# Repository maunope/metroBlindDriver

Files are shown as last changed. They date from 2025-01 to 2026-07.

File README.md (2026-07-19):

# Disclaimer
This is still a prototype; the circuit design was built and tested on a perfboard, the KiCad board design was never tested. Use at your own risk and plz **don't come whining if you damage stuff or set your house on fire.**

# WARNING
This project entails working with a 220V powered device with a metal chassis and **no grounding**. These devices are 40+ years old and saw lots of abuse; wire insulation may fail, and motor windings may short circuit. Before wiring anything up, check impedance between the chassis, the engine hull, and all contacts carrying 220V power; anything below 2 megaohms means insulation needs to be re-checked. 
Consider wiring the blind chassis to the ground line for additional safety.

# Metro Blinds Driver

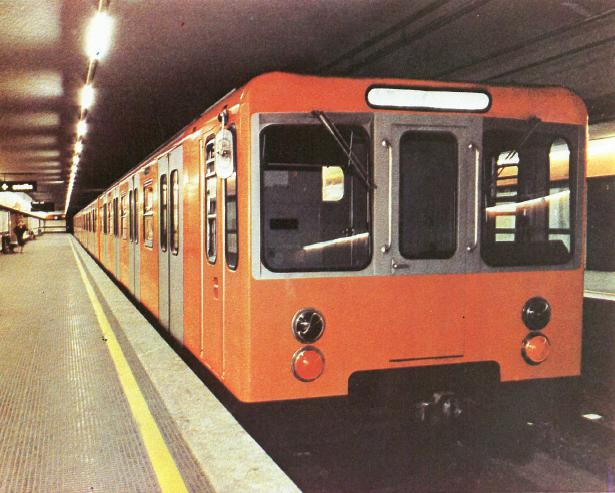
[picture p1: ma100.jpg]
Actotral MA100 vintage photo


Arduino-based driver board to control Acotral MA100 electric locomotives' front and side stops blinds.

Acotral MA100s were first issued to Rome's **"A"** metro line where they were in service between 1980 and 2005, before being overhauled/modified and reassigned to the Roma Lido line until their decommissioning in 2018. 

[Trasporti di Roma](https://romaatac.altervista.org/mezzi-di-roma/ma-100/)
[Wikipedia](https://it.wikipedia.org/wiki/Elettromotrici_ACOTRAL_MA_100)

Stops signaling blinds coming from wagon dismantling started circulating among flip clock collectors and have become a somewhat common find on online marketplaces.

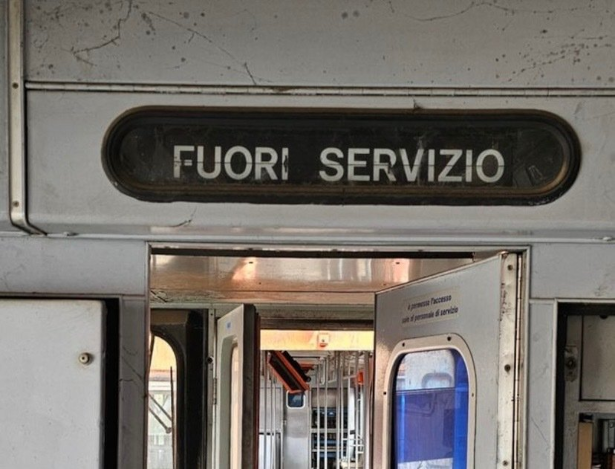
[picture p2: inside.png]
Actotral MA100 inside


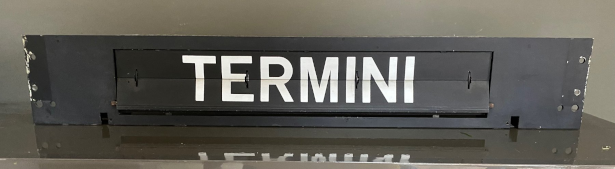
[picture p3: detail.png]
Actotral blind detail


Blinds are controlled through a 7-bit string identifying stops and are powered at 110V AC (motor) / 48V DC (control). This project emulates original locomotive control signals to drive them and display stops.

The board design in this project runs 5V DC control signals and 220V power; it requires minimal modifications to the original blinds' wiring. It is fairly easy, however, to adapt it to run 48V/110V to 100% preserve the integrity of the original wiring.

## Main features   
- Runs through stops using the blind's internal motor
- Allows manual stop selection or programmed stops sequence mode
- Allows saving configurations to the Arduino EEPROM
- Implements several controls to prevent damage/overheating in case of malfunctions

## Lateral blind design
The `LATERAL_BLIND` compile flag enables a command table built for smaller punched rollers found on side-mounted train blinds. This mode is intended to address blinds with smaller punched rollers, those mounted on the side of trains rather than the larger frontal rollers.

On the specimen I tested, the pinout was different compared to the larger frontal roller, but this may not always be true. If your roller is different, you may need to recreate the command array for your exact roller.

## Manual vs. Program mode

In **manual mode** (default), stops are selected through serial port commands or single button presses. The board LED is lit during Manual mode. 

**Program mode** automatically loops a sequence of stops, one step every hour by default. The program will be resumed from the last reached stop in case of power OFF/ON; the hourly step timer will be reset. The board LED is off during Program mode.

To switch between modes, either use serial commands or press the board button for **3 seconds**. 

## Dependencies

- EEPROM (comes with Arduino IDE)
- [Rocket Scream Low Power](https://github.com/rocketscream/Low-Power)

## Arduino circuit board

Check the schematic in this repo; I've built and tested it on perfboard. The board design might not be 100% correct, and the layout could definitely use some improvement.

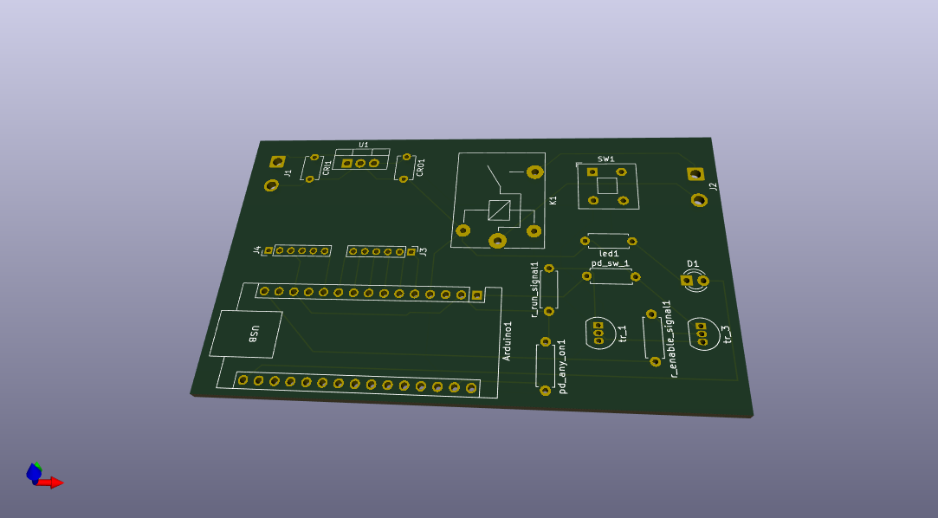
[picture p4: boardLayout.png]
Arduino Board layout


**How to read LED signals**

Either for good or bad news, the Arduino board LED will flash. 

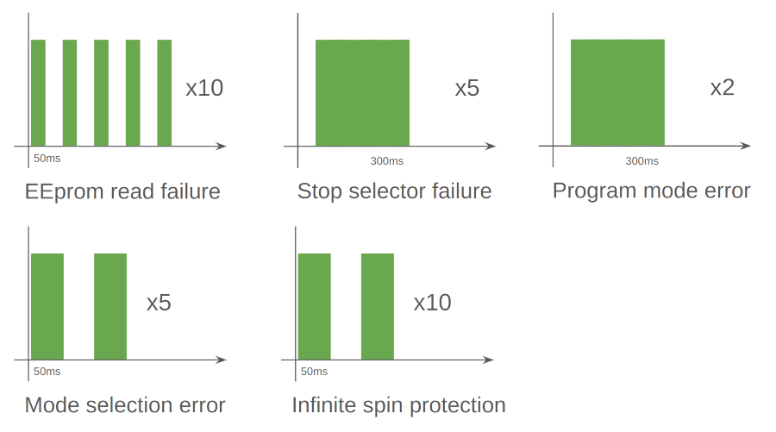
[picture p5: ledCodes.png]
Led error codes


## Original electromechanical control logic 

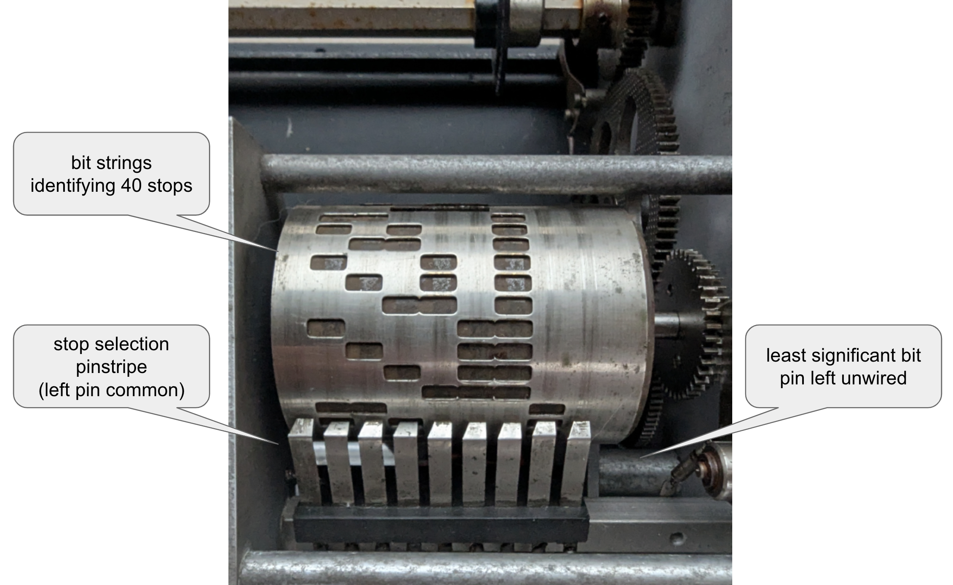
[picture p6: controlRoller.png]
Control roller detail


A punched roller is used to encode 40 unique blind positions. When a string of bits is applied to the pinstripe, the motor spins until the holes combination under the pinstripe matches powered pins, i.e.:

- **0b00111000** bit string corresponding to Termini station is applied to the pinstripe, powering pins 4, 5, 6 from the left (1st left pin is common)
- **0b0011110** bit string on the control roller is under the pinstripe; current flows through pins 4, 5, 6, and the motor spins
- Next roller bit string is **0b0100110** on the control roller; current flows through pin 6, and the motor keeps spinning
- The roller bit string is now **0b11000111**; all 1s on the pinstripe match a 0 on the roller, no current flows, the motor **stops** and will remain still until a different bit string is selected.

The original control board has 7 control pins, 2 relay coil pins, and 2 motor power pins, exposed through a DIN 41622 male connector on the side or back panel.

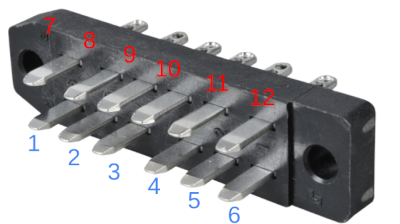
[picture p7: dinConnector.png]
Din connector detail


The original wiring:
- Pin 1-6 and 12: stop selection bit string
- Pin 11: unwired
- Pin 10: 110V AC to relay interrupted line
- Pin 9: Relay coil (+48V signal from selection roller return line)
- Pin 8: Relay coil N
- Pin 7: 110V returning from motor

## Blind Board schematic and modifications

The blind board schematic is available in "metroBlindDriver blind board" KiCad design:

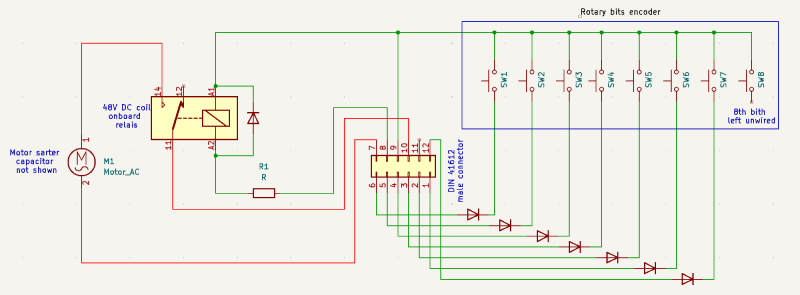
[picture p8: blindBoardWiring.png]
Original blind schematic


In the original blind design, 48V DC bits would be fed into pins 1-6 and 12; they would reach the control roller through diodes and would power the 48V relay coil through the roller common pin until the desired stop was reached. 

The original blind wiring can be easily modified to accept standard household 220V AC power and 5V DC signals.

**IMPORTANT**: Don't use this board design with 48V signals to avoid damage and fire hazard!

**IMPORTANT**: Don't run 220V AC through the motor before its coils are wired in series to avoid damage and fire hazard!

**220V AC motor wiring** Wire the motor as shown in the picture below to drive it with 220V AC power. Plastic motor caps on most (all?) blinds have diagrams explaining how to wire coils in series/parallel.
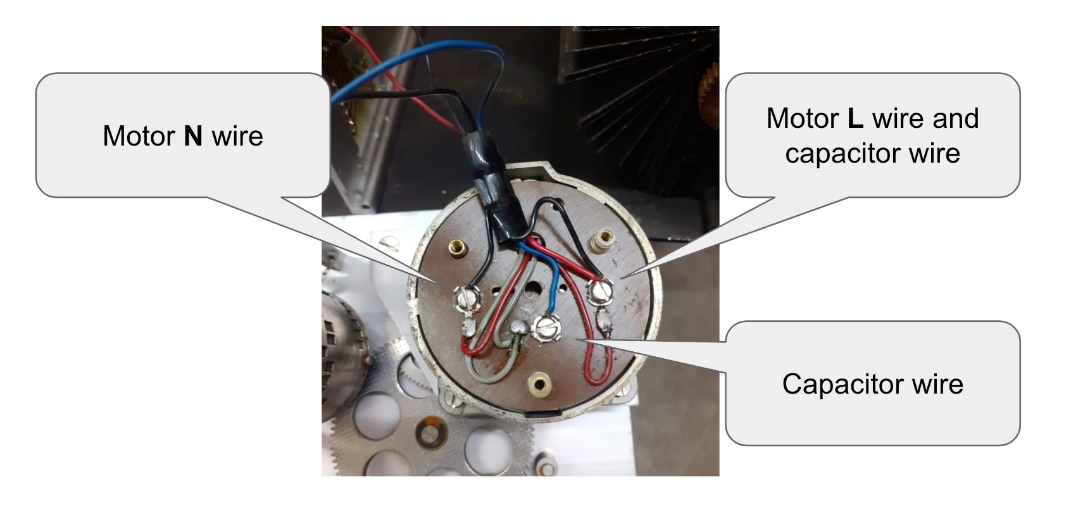
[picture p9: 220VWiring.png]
220V motor wiring detail


**5V DC external relay wiring**

To bypass the 48V coil and use an external relay, clip the motor **N** wire from the connector board trace (board end, not motor end!) and solder it to the top left pin on the DIN connector. If in doubt, use the only pin trace with no wires attached. 

Replacing the original 48V relay with a 5V or 12V one isn't sufficient, as the coil has a 4kohm resistor wired in series; plus, compatible relays are out of production, hard to source, and quite expensive. 

I wanted to preserve the original circuitry as much as possible, but definitely didn't want to faff with 48V signals.
I figured since I had already wired the motor for 220V AC, another small modification wouldn't matter much, and moving a wire to a different pin seemed way less invasive than replacing a relay and a big *ss resistor.
You might want to do things differently here; the circuit is easy enough to work with, these are just my 2c :-) 

Rewired schematic below:

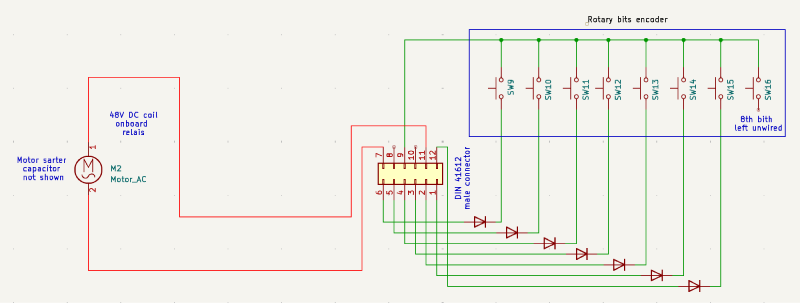
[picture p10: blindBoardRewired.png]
Original blind schematic


The new wiring:
- Pin 1-6 and 12: 5V bit string
- Pin 11: to motor relay NO contact on Arduino board
- Pin 10: unwired, can be used to ground the blind chassis
- Pin 9: to Arduino "Any Running" pin
- Pin 8: unwired
- Pin 7: to motor relay NO contact on Arduino board

## How to install and adjust

**First things first, let's not fry stuff**

- Check wirings and voltages
- **Mandatory**: rewire the blind board to use an external 5V relay; **don't use 48V signals with this Arduino board design!**
- **Optional**: rewire the motor to run on 220V AC; if you happen to have a 110V AC power source, that will work fine
- Wire the DIN connector pins; be sure not to short circuit anything
- Power the board and the motor **L** wire
 **No smoke? Good.**

By default, the controller will wait for commands in manual mode with the board LED **ON**.

- Press the board button briefly; the blind should roll one stop forward
- (Optional) press the board button for 3 seconds to switch to Program mode

## Push buttons commands

- **Brief press:** move one stop forward
- **3 seconds press:** switch between Manual and Program mode

## Serial port commands

Commands format: **(<<|>>)[A-Z,0-9]+**

- **<<** to read info, **>>** to set
- Command name, in caps
- (Where applicable) parameters

One command per line; the parser is pretty crude, please stick to tested commands ;-) 

**Available commands**:

- **>>GO[0-9][0-9]** select stop by zero-padded two-digit number, 01-40 (only works in manual mode)
- **>>(stop name)** (i.e., >>ANAGNINA, >>CINECITTA) select stop by name (only works in manual mode)
- **>>STOP** halt the motor
- **>>RUN** continuously run the motor 
- **>>PROGRAMSTEPSSECONDS[0-9]{4}** write steps duration for program mode, zero-padded four digits
- **<<PROGRAMSTEPSSECONDS** read steps duration for program mode
- **>>DEFAULTPROGRAM** load the default stops program to memory
- **>>PROGRAMSTOPS[0-9][0-9](?:[0-9][0-9]){0,39}** write program mode stops sequence, zero terminated, up to 40 zero-padded two-digit positive integers. The sequence is required to be ascending (i.e., 1-2-3 valid, 1-3-2 not valid)
- **<<PROGRAMSTOPS** print the program stops sequence currently in memory
- **>>PROGRAMMODE** switch to Program mode
- **>>MANUALMODE** switch to Manual mode (default)
- **>>RESETDEFAULTS** reset default configuration 
- **<<EEPROMDATA** print current eeprom conf
- **>>EEPROMDATA** write current conf from ram to eeprom
- **<<POSITION** print the current blind roller position
- **<<COMPILEDATETIME** print the sketch build timestamp

## Build flags

-DEBUG_MODE enable serial port debug messages, disable sleep mode

## Unreachable stops

The control roller pinstripe 8 signals encode 40 unique bit strings, each with three raised bits (i.e., 0b11001000, 0b00110010). This allows moving from any stop to any other by applying the destination code bit string to stop selection pins. 

At least, this is how the control roller would work hadn't its original designers decided to leave the rightmost pin unwired.

As a result, 5 out of 40 stops are encoded by only 2 wired pins and only work when selected starting from the 13 stops right behind them. 
The matrix below highlights misencoded stops and the stops that would be wrongly displayed when their code is used, i.e.:

- The blind displays stop **2** (code **0b1000110**)
- Stop **21** (code **0b1100000**) is selected
- The blind spins until stop **6**, (code **0b1100001**)
- The bitwise "(input bit string) **AND NOT** (roller bit string)" of stops **21** and **6** codes is 0 -> the relay coil is not powered
- The blind stopped on stop **6** before reaching **21** and would halt on 26, 27, 30 and 37 due to the same reason
- (**Note:** code **0b1100000** correctly drives the blind to stop **21** starting from stops 7-20)

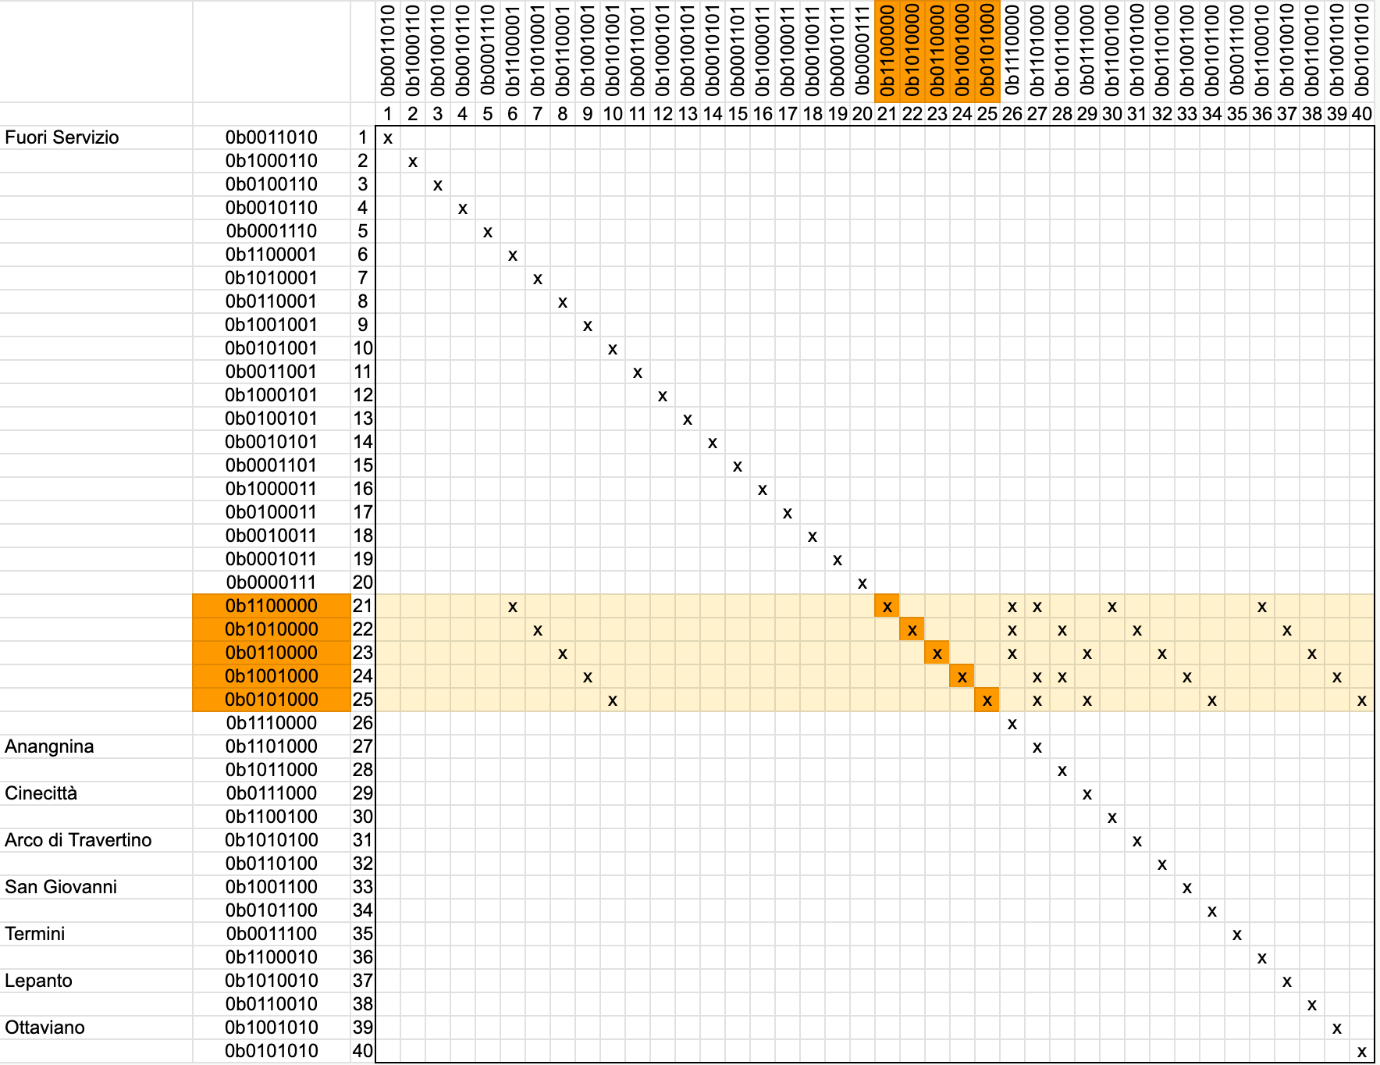
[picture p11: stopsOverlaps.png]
Overlapping stop codes table


This behavior **did not** affect actual service on Roma Metro **A** as the 5 impacted stops were blank. I decided to leave it unchanged as an interesting quirk of the original design; you might want to fix it if you plan to display anything on stops 21-25 :-D 

## Troubleshooting

**Q:** I can't tell what's going on with EEPROM data.

**A:** The <<EEPROMDATA command can extract all the info saved on the EEPROM.

**Q:** I keep getting "nonexistent stop" error.

**A:** Check wiring; any short circuit? Any missing wire? 

**Q:** Motor buzzes and doesn't spin! What's wrong?

**A:** Have you rewired the motor correctly? 

**Q:** I rebooted the board, and all my configurations are lost.

**A:** Run >>EEPROMDATA to persist configuration on EEPROM.

**Q:** I have disassembled the punched roller and now it doesn't stop on the right positions.

**A:** If the roller is misaligned, it will not work correctly. The solution is to disassemble it again, align it to the right stop, and reassemble it. It is possible to fine tune it by undoing the screw on the roller side and moving the outer plate slightly.

**Q:** That PCB design is **lame**!

**A:** It is. Any help much appreciated! ;-)

## Todo
- Readme completion
- Circuit board layout improvement

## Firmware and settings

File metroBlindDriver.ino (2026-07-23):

#include <LowPower.h>                //https://github.com/rocketscream/Low-Power
#include <EEPROM.h>

// Uncomment the next line to switch to the lateral-blind command table.
#define LATERAL_BLIND
//#define DEBUG_MODE



#ifdef LATERAL_BLIND
const int MAX_STOPS = 30;
#else
const int MAX_STOPS = 40;
#endif



struct ProgramModeStatus
{
  //current program mode position index to be displayed
  int programPos = -1;
  //last succesfully displayed destination
  int lastReachedProgramPos = -1;
  //last recorded movement millis
  unsigned long lastMovementMillis = 0;
  byte stops[MAX_STOPS] = {};
  byte stopsLength = 0;
  int stepsSeconds = -1;
};


struct ManualModeStatus
{
  //manual mode status variables
  int lastReachedManualStop = -1;
};

struct Signals
{
  //bit string currently set on output pins
  byte bitString = 0b00000000;
  //manual/program mode
  int mode = -1;
  //motion enabled status,
  bool motionEnabled = false;
};

struct EEpromData
{
  int mode = -1;
  byte programStops[MAX_STOPS];
  byte programLength = 0;
  int programStepsSeconds = -1;
};



//debug mode redirects stdout to the serial port, this avoids the need for strings buffering
#ifdef DEBUG_MODE
// Define a custom putchar function to redirect output to Serial
int putCharToSerial(char c, FILE *stream) {
  if (stream == stdout) { // Check if it's standard output
    Serial.write(c);
  }
  return 0;
}

// Declare a FILE stream for stdout (no initializer here!)
FILE customStdOut;
//printf macro, together with putCharToSerial driver debug messages straight to the Serial port,
//stores string in Program Memory and appends a new line to each log line automatically
#define DEBUG_PRINTF(format, ...) printf_P(PSTR(format "\n"),##__VA_ARGS__);
#endif

#ifndef DEBUG_MODE
#define DEBUG_PRINTF(format, ...) // Nothing 
#endif

//automatic program based movement or manual stop selection
const int MANUAL_MODE = 0;
const int PROGRAM_MODE = 1;



//8 bits strings corresponding to each Roma Metropolitana A blind position
//rightmost bit is not relevant as the corresponding pin on the blind bit strings roller is not connected
//sorting mirrors the punch hole roller's, first element selection ("Fuori Servizio") is arbitrary
//first (0000000) and last (1111111) strings are "set all pins LOW/HIGH" commands, which have no correspondance on the roller
//NOTE: the two COMMANDS[] tables below  use different byte values for the same stop names.
//We double-checked the stop codes and they are not just reversed or simple bit-shifted variants of each other;
//they are different encodings between the two branches, so the code must keep both tables separate.

#ifdef LATERAL_BLIND
const byte COMMANDS[] = {
  0b00000000,  // 00 (Stop the blind, wherever it is)
  0b01001010, //1 ANAGNINA
  0b00101010, //2
  0b00011010, //3 CINECITTA
  0b11100000, //4
  0b11010000, //5 ARCODEITRAVERTINO
  0b10110000, //6 
  0b01110000, //7 SANGIOVANNI 
  0b11001000, //8
  0b10101000, //9 TERMINI
  0b01101000, //10
  0b10011000, //11 LEPANTO
  0b01011000, //12
  0b00111000, //13 OTTAVIANO
  0b11000100, //14 
  0b10100100, //15 FUORI SERVIZIO
  0b01100100, //16 BUONE
  0b10010100, //17 
  0b01010100, //18 BUONE
  0b00110100, //19 VACANZE
  0b10001100, //20 
  0b01001100, //21 ANCHE A TE
  0b00101100, //22 E FAMIGLIA
  0b00011100, //23 
  0b11000010, //24 
  0b10100010, //25
  0b01100010, //26
  0b10010010, //27
  0b01010010, //28
  0b00110010, //29
  0b10001010, //30
  0b11111111   // 31 (Run the blind, wherever it is)
};
const int COMMANDSLEN = 32;
const int STOP = 0;
const int ANAGNINA = 1;
const int CINECITTA = 3;
const int ARCODITRAVERTINO = 5;
const int SANGIOVANNI = 7;
const int TERMINI = 9;
const int LEPANTO = 11;
const int OTTAVIANO = 13;
const int FUORISERVIZIO = 15;
const int RUN = 31;

//19 BUONE
//20 VACANZE
//22 ANCHE A TE
//23 E FAMIGLIA

#else
const byte COMMANDS[]  = {
  0b00000000,  // 00 (Stop the blind, wherever it is)
  0b00110100,  // 01 Fuori servizio 
  0b10001100, 0b01001100, 0b00101100, 0b00011100, 0b11000010, 0b10100010, 0b01100010, 0b10010010, //02-26 blank  space
  0b01010010, 0b00110010, 0b10001010, 0b01001010, 0b00101010, 0b00011010, 0b10000110, 0b01000110,
  0b00100110, 0b00010110, 0b00001110, 0b11000000, 0b10100000, 0b01100000, 0b10010000, 0b01010000,
  0b11100000,
  0b11010000,  // 27 Anagnina
  0b10110000,
  0b01110000,  // 29 Cinecittà
  0b11001000,
  0b10101000,  // 31 Arco di Travertino 
  0b01101000,
  0b10011000,  // 33 San giovanni 
  0b01011000,
  0b00111000,  // 35 Termini 
  0b11000100,
  0b10100100,  // 37 Lepanto 
  0b01100100,
  0b10010100,  // 39 Ottaviano 
  0b01010100,
  0b11111111   // 41 (Run the blind, wherever it is)
};
//the blind has 40 stops, and this is going to change :-)
const int COMMANDSLEN = 41;

//indexes of Roma Metropolitana A stops
const int STOP = 0;
const int FUORISERVIZIO = 1;
const int ANAGNINA = 27;
const int CINECITTA = 29;
const int ARCODITRAVERTINO = 31;
const int SANGIOVANNI = 33;
const int TERMINI = 35;
const int LEPANTO = 37;
const int OTTAVIANO = 39;
const int RUN = 41;
#endif

//map pins to bit string positions, 0 ot 6
//const int PIN_MAP[] = { 3, 4, 5, 6, 7, 8, 9 };
const int PIN_MAP[] = { 9, 8, 7, 6, 5, 4, 3 };

//10 seconds are approx. 2.5 full revolutions
const int MAX_CONTINUOS_RUN_SECS = 10;

//start in manual mode by default, save eeprom conf to start program mode at startup
const int DEFAULT_MODE = MANUAL_MODE;

//seconds between each autonomous blind step
const int DEFAULT_SECONDS_BETWEEN_STEPS = 3600;

const long int SECONDS_PER_DAY = 86400;


const int RUNNING_PIN = 0;  //Reads high when the blind is rotating
const int PUSH_BUTTON_PIN = 1;
const int ENABLE_PIN = 10;  //Set to HIGH to enable the output relais coil
const int FEEDBACK_LED_PIN = 14;

//output signal status and current mode stored here, at all times this
// variable represents the desired status configured on output pins
Signals signals;

//status for program and manual mode, i.e. "reached stop X", "last movement recorded on Y"
ProgramModeStatus programModeStatus;
ManualModeStatus manualModeStatus;
unsigned long movementStartedMillis = 0;

unsigned long lastCommandReceived = 0;

//this default program cycles stops from Anagnina to Fuori servizio
#ifdef LATERAL_BLIND
const byte DEFAULT_PROGRAM[MAX_STOPS] = {1, 3, 5, 7, 9, 11, 13, 15, 16, 17, 19, 20, 22, 23};
byte DEFAULT_PROGRAM_LENGTH = 14;
#else
const byte DEFAULT_PROGRAM[MAX_STOPS] = {27, 29, 31, 33, 35, 37, 39,  01};
byte DEFAULT_PROGRAM_LENGTH = 8;
#endif


// how long the push button has been pressed
unsigned long pushButtonPressedMillis = 0;

EEpromData eepromData;

bool forceMoveToNextProgramStop = false;
unsigned long lastPositionLogMillis = 0;

// Forward declarations for functions defined later in the sketch.
void setStopSelector(byte newBitString, Signals& signals);
void stopBlind(Signals& signals);
void runBlind(Signals& signals);
bool setMotionEnabled(bool enable, Signals& signals);
byte readBlindPosition(Signals& signals);
void parseSerialCommands(char command[], Signals& signals, ProgramModeStatus& programModeStatus, ManualModeStatus& manualModeStatus);
void moveProgramToClosestStop(ProgramModeStatus& programModeStatus, Signals& signals);
void setMode(int newMode, Signals& signals, ProgramModeStatus& programModeStatus, ManualModeStatus& manualModeStatus);

//resets default configuration and stops the blind,  doesn't persist data to eeprom
void resetDefaults(Signals& signals, ProgramModeStatus& programModeStatus, ManualModeStatus& manualModeStatus)
{
  stopBlind(signals);
  setMode(DEFAULT_MODE, signals, programModeStatus, manualModeStatus);
  memcpy(programModeStatus.stops, DEFAULT_PROGRAM, sizeof(DEFAULT_PROGRAM));
  programModeStatus.stopsLength = DEFAULT_PROGRAM_LENGTH;
  programModeStatus.stepsSeconds  = DEFAULT_SECONDS_BETWEEN_STEPS;
}

//writes current conf to eeprom, no validation
int writeConfToEEprom(Signals signals, ProgramModeStatus programModeStatus)
{
  EEpromData eepromData;
  eepromData.mode = signals.mode;
  memcpy(eepromData.programStops, programModeStatus.stops, sizeof(programModeStatus.stops));
  eepromData.programLength = programModeStatus.stopsLength;
  eepromData.programStepsSeconds = programModeStatus.stepsSeconds;
  EEPROM.put(0, eepromData);
}

//loads configuration from eeprom  (doesn't apply it though!), return 0 on success, -1 on faulty data
int loadConfFromEEprom(EEpromData& eepromData)
{
  int exitStatus = 0;
  EEPROM.get(0, eepromData);
  if (eepromData.mode != MANUAL_MODE && eepromData.mode != PROGRAM_MODE) {
    DEBUG_PRINTF("Corrupted EEProm data, invalid mode, reverting to default mode");
    eepromData.mode = DEFAULT_MODE;
    exitStatus = -1;
  }
  if (eepromData.programStepsSeconds < 0) {
    DEBUG_PRINTF("Corrupted EEProm data, invalid program mode interval, reverting to default value");
    eepromData.programStepsSeconds = DEFAULT_SECONDS_BETWEEN_STEPS;
    exitStatus = -1;
  }
  if (eepromData.programLength > MAX_STOPS) {
    DEBUG_PRINTF("Corrupted EEProm data, invalid program length, reverting to 0");
    eepromData.programLength = 0;
    exitStatus = -1;
  }
  for (int i = 0; i < eepromData.programLength; i++) {
    if (eepromData.programStops[i] <0  || eepromData.programStops[i] >= COMMANDSLEN) {
      DEBUG_PRINTF("Corrupted EEProm data, invalid stop selection in program, reverting to blank program");
      exitStatus = -1;
    }
  }
  return exitStatus;
}

// blinks the feedback led alternating given on/off time, for the given number
// of times.
void blinkFeedbackLed(int onMillis, int offMillis, int iterations) {
  int previousState = digitalRead(FEEDBACK_LED_PIN);
  for (int i = 0; i < iterations; i++) {
    digitalWrite(FEEDBACK_LED_PIN, HIGH);
    delay(onMillis);
    digitalWrite(FEEDBACK_LED_PIN, LOW);
    delay(offMillis);
  }
  digitalWrite(FEEDBACK_LED_PIN, previousState);
}


//writes the 8 digits padded BIN  representation of a byte in a given 9bytes buffer and returns its pointer for your convenience :-)
char* getPaddedBin(byte bitString, char buf[]) {
  for (int i = 7; i >= 0; i--) {
    buf[7 - i] = (bitString & (1 << i)) ? '1' : '0';
  }
  buf[8] = '\0';
  return buf;
}

//returns its index in commands array if a given bitString exists on the control signals roller, or -1 if it doesnt
int positionExists(byte bitString)
{

  for (int i = 0; i < COMMANDSLEN; i++) {
    if (COMMANDS[i] == bitString) {
      return i;
    }
  }
  return -1;
}


//outputs a bitString to blind control signal pins and saves it as the current one
//this method won't reset pins once the requested position is reached
//this method doesn't check the existance of the requested newBitString
void setStopSelector(byte newBitString, Signals& signals) {
  //note that hte least significant bit is never used, as there's no pin using it
  if (newBitString != signals.bitString) {
    for (int i = 7; i >= 1; i--) {
      digitalWrite(PIN_MAP[7 - i], ((newBitString >> (i)) & 1) == 1 ? HIGH : LOW);
    }
    signals.bitString = newBitString;
  }
}



//sends a stop command to the blind, regardless of its position
void stopBlind(Signals& signals) {
  setStopSelector(COMMANDS[STOP], signals);
}


//sends a run command to the blind, regardless of its position,
//motion will continue until a different command is sent or enable pin is set to low
void runBlind(Signals& signals) {
  setStopSelector(COMMANDS[RUN], signals);
}


//enables/disables blind movement
bool setMotionEnabled(bool enable, Signals& signals) {
  digitalWrite(ENABLE_PIN, enable ? HIGH : LOW);
  signals.motionEnabled = enable;
}

//reads the current blind position,disabling motion temporarily
//this method doesn't check if the blind is rolling before stopping it
//this method doesn't check if the returned position exists in the roller
//this method restores the pre-existing blind status (selected stop and enable status) before returning
byte readBlindPosition(Signals& signals) {

  char binBufA[9];
  char binBufB[9];
  byte savedBitString = signals.bitString;
  bool savedMotionEnabled = signals.motionEnabled;

  //temporarily disbale motion, to ensure a consistent reading and avoid unwanted movement
  setMotionEnabled(false, signals);

  byte currentPosition = 0;
  stopBlind(signals);
  //only 7 as we're cycling on pins, but then we need to shift 8
  for (int i = 0; i < 7; i++) {
    digitalWrite(PIN_MAP[i], HIGH);
    delay(5);
    //inverts (HIGH outputs 0, LOW outpus 1), for easier readability/debugging this method represents stops bit strings as the corresponding selector bit string
    //Actually, if the selected bitString is 11001100, motion stops on 00110011 configurationon of the blind roller
    //(motion stop when bitwise AND between selected string and rolles string is 0)
    currentPosition |= ((digitalRead(RUNNING_PIN) == HIGH ? 0 : 1) << (7 - i));
    digitalWrite(PIN_MAP[i], LOW);
    delay(5);
  }
  //reset previous state
  setStopSelector(savedBitString, signals);
  setMotionEnabled(savedMotionEnabled, signals);
  //DEBUG_PRINTF("readBlindPosition returning: %s", getPaddedBin(currentPosition, binBuf));
  return currentPosition;
}
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
void loop() {
  delay(50);
  char binBufA[9];
  char binBufB[9];

  // self reset every week, just in case I f*cked up and some variable would
  // overflow left unchecked (i.e. millis)
  if (millis() / 1000 >= SECONDS_PER_DAY * 7) {
    asm volatile("  jmp 0");
  }

  #ifdef DEBUG_MODE
  if ((millis() - lastPositionLogMillis) >= 2000) {
    lastPositionLogMillis = millis();
    byte loggedPosition = readBlindPosition(signals);
    DEBUG_PRINTF("Roller position: %s (%d)", getPaddedBin(loggedPosition, binBufA), loggedPosition);
  }
  #endif

  if (Serial.available() > 0) {
    char command[128];
    int i = 0;
    while (Serial.available() > 0 && i < 127) {
      char c = Serial.read();
      if (c == '\n') {
        break;  // Break when newline character is received
      }
      command[i] = c;
      i++;
    }
    command[i] = '\0';
    parseSerialCommands(command, signals, programModeStatus, manualModeStatus);
    lastCommandReceived = millis();
  }

  //current blind position, unknown until read from the roller
  byte currentBlindPosition = 0;

  ///
  /// Program mode:
  /// - Check what the next step is
  //  - if last reached position is behind the current selected and the delay between steps has elapsed, Enable motion to the desired stop
  //  - (Loop repeats until rotation stops, signals generation are reiterated on each loop)
  //  - rotation is stopped, check if a valid position has been reached, and move on to the next step in the program
  //  - sleep (TODO make a non blockng one)
  if (signals.mode == PROGRAM_MODE) {

    if (programModeStatus.programPos == -1) {
      //at boot we need to recover what the next position is
      moveProgramToClosestStop(programModeStatus, signals);
      DEBUG_PRINTF("Recovering next program position: %d", programModeStatus.programPos);
    }
    if (programModeStatus.programPos == -1){
       //if programPos is still equals -1, we failed to read a valid position, likely the roller was halted amidsts two stops, let's just restart from 0 then
       programModeStatus.programPos = 0;
       DEBUG_PRINTF("Resetting program mode pos to 0");
    }

    if (programModeStatus.programPos >= 0 ) {

      //program mode enters once in this clause to trigger movement,
      //-> last reached stop is behind the current programmed, and at least stepSeconds seconds have passed since last movement -> movement is triggered
      //-> the blind keeps moving
      //-> next iterations, lastReached still behind, lastMovement sitll > stepSeconds ago, we keep confirming movement
      //-> UNTIL the blind isn't moving, Eureka! programmed stop reached!, we update program pos and last reached stop, and last movement millisecond
      //-> on next iteration, we won't enter this IF clause, till the steps interval has expired
      //
      //
      // OR
      //
      // there's a forced movement to make
      // we keep entering regardless of elapsed milliseconds
      // same as previous case, but we don't update last movement timestamp

      if ((programModeStatus.lastReachedProgramPos  < programModeStatus.programPos &&  ((millis() - programModeStatus.lastMovementMillis) > ((unsigned long)programModeStatus.stepsSeconds * 1000))) || forceMoveToNextProgramStop == true) {
        setMotionEnabled(true, signals);
        //move to the desired position
        DEBUG_PRINTF("Starting movement to reach %d %d %d", programModeStatus.programPos, programModeStatus.stops[programModeStatus.programPos], COMMANDS[programModeStatus.stops[programModeStatus.programPos]]);
        setStopSelector(COMMANDS[programModeStatus.stops[programModeStatus.programPos]], signals);

        //not running, maybe requered stop was received
        if (digitalRead(RUNNING_PIN) == LOW) {
          setMotionEnabled(false, signals);
          currentBlindPosition = readBlindPosition(signals);
          //requested stop reached
          if (currentBlindPosition == signals.bitString) {
            //advance one step and handle rollover to program start
            programModeStatus.lastReachedProgramPos = programModeStatus.programPos;
            programModeStatus.programPos =  (programModeStatus.programPos == programModeStatus.stopsLength - 1) ? 0 : programModeStatus.programPos + 1;
            programModeStatus.lastReachedProgramPos = programModeStatus.programPos > 0 ? programModeStatus.lastReachedProgramPos : -1;
            DEBUG_PRINTF("New program pos reached %d, programpos %d", programModeStatus.lastReachedProgramPos, programModeStatus.programPos);
          } else {
             DEBUG_PRINTF("Requested position not reached, but blind not moving, possible malfunction (selected a stop between 21 and 25 maybe? checkk \"Unreachable Stops\" in deocumentation for details)");
             blinkFeedbackLed(300, 50, 5);
          }
          DEBUG_PRINTF("Stopped at: %s bitString: %s",  getPaddedBin(currentBlindPosition, binBufA), getPaddedBin(signals.bitString, binBufB));
          stopBlind(signals);

          //if we came here following a button command, don't reset time till next step
          if (forceMoveToNextProgramStop == false) {
            programModeStatus.lastMovementMillis = millis();
          } else {
            forceMoveToNextProgramStop = false;
          }
        }
      }
    }
    else {
      DEBUG_PRINTF("ERROR, could not recover program position");
       blinkFeedbackLed(300, 50, 2);
       delay(2000);
    }

  } else if (signals.mode == MANUAL_MODE) {
    setMotionEnabled(true, signals);
    setStopSelector(signals.bitString, signals);
    if (digitalRead(RUNNING_PIN) == LOW) {
      setMotionEnabled(false, signals);
      currentBlindPosition = readBlindPosition(signals);
      //requested stop reached
      if (currentBlindPosition == signals.bitString) {
        manualModeStatus.lastReachedManualStop = currentBlindPosition;
        DEBUG_PRINTF("Stopped in manual mode at: %s, bitString: %s)", getPaddedBin(currentBlindPosition, binBufA), getPaddedBin(signals.bitString, binBufB));
      } else if (manualModeStatus.lastReachedManualStop != currentBlindPosition) {
        DEBUG_PRINTF("Requested position not reached, but  blind not moving, possible malfunction (selected a stop between 21 and 25 maybe? check \"Unreachable Stops\" in deocumentation for details)");
        blinkFeedbackLed(300, 50, 5);

      }
        stopBlind(signals);
    }
  } else {
    DEBUG_PRINTF("ERROR, unknown mode: %d", signals.mode);
     blinkFeedbackLed(100, 100, 10);
     delay(2000);
  }

  int currentPositionIndex = positionExists(currentBlindPosition);
  //If we have stopped in some non existent place, let the user know
  if (currentPositionIndex < 0 && digitalRead(RUNNING_PIN) == LOW && currentBlindPosition > 0) {
    DEBUG_PRINTF("Blind not moving, but detected a non existant roller contacts status %s, possible malfunction", getPaddedBin(currentBlindPosition, binBufA));
    blinkFeedbackLed(300, 50, 5);
  }

  //track how long we've been moving the roller, protect from infinites loops
  movementStartedMillis = (digitalRead(RUNNING_PIN) == LOW ? 0 : ((movementStartedMillis == 0) ? millis() : movementStartedMillis));
  //give and error message and reset in case we've exceeded the maximum allowed uninterrupted run time
  if ((millis() - movementStartedMillis) / 1000 > MAX_CONTINUOS_RUN_SECS && movementStartedMillis > 0) {
     DEBUG_PRINTF("Maximum continuous run exceeded, %d seconds, max allowed: %d pausing for 30seconds and rebooting", ((millis() - movementStartedMillis) / 1000), MAX_CONTINUOS_RUN_SECS);
     setMotionEnabled(false, signals);
     stopBlind(signals);
     blinkFeedbackLed(100, 100, 20);
     delay(30000);
     asm volatile("  jmp 0");
  }


  //two button press commands:
  //3 seconds, switch mode
  //brief, advance 1 step, in manual mode it's 1 stop jump, in program next stop in the program sequence
  if (digitalRead(PUSH_BUTTON_PIN) == HIGH) {
    if (pushButtonPressedMillis == 0) {
      pushButtonPressedMillis = millis();
    }
    // long press
    else if (millis() - pushButtonPressedMillis >= 3000) {
      lastCommandReceived = millis();
      // this totals to 1 second
      blinkFeedbackLed(100, 100, 5);
      if (signals.mode == PROGRAM_MODE) {
        setMode(MANUAL_MODE, signals, programModeStatus, manualModeStatus);
        DEBUG_PRINTF("Manual mode set through button press");
      }
      else {
        setMode(PROGRAM_MODE, signals, programModeStatus, manualModeStatus);
        DEBUG_PRINTF("Program mode set through button press");
      }
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

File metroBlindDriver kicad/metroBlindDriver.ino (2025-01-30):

#include <Arduino.h>


int pinMap[]={3,4,5,6,7,8,9};

bool last=LOW;
void setup() {
  Serial.begin(9600);
  // Set pins 2 to 8 as outputs
  for (int i = 0; i < 7; i++) { 
    pinMode(pinMap[i], OUTPUT); 
  }
  pinMode(0, INPUT);  //ANYRUNNING
  
  pinMode(1, INPUT);  //BUTTON

  pinMode(10, OUTPUT); //DISABLE
  pinMode(14, OUTPUT); //LED
  
}

void setOutput(char* bits)
{

  for (int i = 0; i < 7; i++) { 
    int value=bits[i]=='1'?HIGH:LOW;
    digitalWrite(pinMap[i],value);
  }
}


 char* command="0000000";

  char* commands[]={
  "0000000"//stop roller
  ,"0011010"// Fuori servizio
  ,"1000110"
  ,"0100110"
  ,"0010110"
  ,"0001110"
  ,"1100001"
  ,"1010001"
  ,"0110001"
  ,"1001001"
  ,"0101001"
  ,"0011001"
  ,"1000101"
  ,"0100101"
  ,"0010101"
  ,"0001101"
  ,"1000011"
  ,"0100011"
  ,"0010011"
  ,"0001011"
  ,"0000111"
  ,"1100000"
  ,"1010000"
  ,"0110000"
  ,"1001000"
  ,"0101000"
  ,"1110000"
  ,"1101000" // 27 Anagnina
  ,"1011000"
  ,"0111000" // 29 Cinecittà
  ,"1100100"
  ,"1010100" // 31 Arco di Travertino
  ,"0110100"
  ,"1001100" // 33 San giovanni
  ,"0101100"
  ,"0011100" // 35 Termini
  ,"1100010"
  ,"1010010" // 37 Lepanto
  ,"0110010"
  ,"1001010" // 39 Ottaviano
  ,"0101010"};


  int program[]={01,27,29,31,33,35,37,39};
  int currentProgramPos=0;

void loop() {

 
  delay(200);
  
  if (Serial.available() > 0) {
    char * commandIndex="   ";
    int i = 0;
    while (Serial.available() > 0 && i < 3) {
      char c = Serial.read();
      if (c == '\n') {
        break;  // Break when newline character is received
      }
      commandIndex[i] = c;
      i++;
    }
    Serial.println("New Command: "+String(commandIndex));
    command=commands[String(commandIndex).toInt()];
  } 
  
  digitalWrite(10,HIGH); 

  command=commands[program[currentProgramPos]];

 
  
  for (int i=0;i<7;i++){
    digitalWrite(pinMap[i],command[i]=='1'?HIGH:LOW);  
  }


  
  int running= digitalRead(0);

   if (running==LOW)
   {
    currentProgramPos=currentProgramPos==7?0:currentProgramPos+1;
   
     
    char current[]="0000000";
    digitalWrite(10,LOW);
    
    delay(100);
    for (int i=0;i<7;i++) //FIXME MAKE 7
    {
      for (int j=0;j<7;j++)
      {
        digitalWrite(pinMap[j],LOW);
      }
      delay(100);
      digitalWrite(pinMap[i],HIGH);
      delay(100);
      //Serial.println(String(digitalRead(0)));
      current[i]=digitalRead(0)==HIGH?'0':'1'; 
    }
    for (int i=0;i<7;i++)
    {
        digitalWrite(pinMap[i],LOW);
    }
    Serial.println("stopped at: "+String(current)+" command: "+String(command));
  
   }
   else
   {
    Serial.println(" Running: "+String(running)+ " command: "+String(command));
   }
  

   
}

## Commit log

2025-02-01 fix to program mode and doc
    [metroBlindDriver.ino]
2025-02-09 - configuration persistence - switch to program mode strings for debug - debug mode write to serial - methods for saving program, mode, program step interval
2025-02-10 added push button commands
2025-02-13 - Added idle mode - Fixed feedback led leaving led in wrong position - Fixed shared buffer for bitstring output bug - Added check to avoid stops programs going backwards - Added <<EEPROMDATA - fixed 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
    [metroBlindDriver.ino]
2025-02-14 updated pcb design
    [metroBlindDriver.kicad_pcb, metroBlindDriver.kicad_sch]
2025-02-14 added board layout image
2025-02-18 added schematics to readme
    [metroBlinDriver blind board.kicad_pcb, metroBlinDriver blind board.kicad_sch]
2025-02-18 led error codes
2025-02-18 fixed led error code
    [metroBlindDriver.ino]
2025-02-21 fixed readme, added sch file
    [metroBlinDriver blind board.kicad_sch]
2025-03-13 fixed bug on sleep mode that put the board to sleep every 5 minutes, implemented reset defaults method, corrected a bug that rewrote conf to eeprom on each setup, implemented serial command to read c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
    [metroBlindDriver.ino]
2025-03-16 fixed a bug on idle mode
    [metroBlindDriver.ino]
2025-03-16 further correction to sleep mode
    [metroBlindDriver.ino]
